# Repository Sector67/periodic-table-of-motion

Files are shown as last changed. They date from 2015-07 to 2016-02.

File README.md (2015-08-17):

# Periodic Table of Motion

## Overview

A science museum needs interactive exhibits, and this is an exhibit that can easily be extended, is easy to setup and install, is robust and safe and easy to maintain. Exhibits can easily cost tens of thousands of dollars, but this one can grow to any size budget but the top of the line is still under $4k. The idea is a periodic table of motion, where each cell, instead of an element, is a type of mechanical motion. Inside the cell is a description of the motion, a button to activate it, and an actual example of a working machine that uses the principle. Simple machines (lever, pulley, gear, etc.) are at the top of each column, and they increase in complexity. For an example of the variety of types of motions I want to capture and show off, see http://507movements.com. This project is very educational and interactive, and distills the basics of mechanics into individual and easy to understand concepts, building on them to show advanced motion and power transfer in a fun way.

## Structure

A cell is the basic independent unit. It has a title, description, machine class, and example use. It also has a physical manifestation which is described with 3D cad files and a bill of materials and build instructions. It also has code to control the display, written in Arduino for an ATTiny.

The repository has a section for cells, which are all based on the template cell. Each subfolder in the cells subfolder is used for a different cell. The template_cell can be copied and extended.

The underlying electronics and enclosure for a cell is defined in the cell subfolder. These instructions are used to build every cell. The cells folder is how to modify that cell to be unique.

The table is the large structure that contains the cells. This can be modified to suit the installation, but the repository contains a sample wall that is 5 cells tall, 12 wide, and contains all the parts necessary for the power supply as well.

The power supply is an ATX computer supply. Sufficiently large installations should use multiple supplies, possibly one for every 3-4 columns, as a typical behavior might be for kids to push all the buttons at once.

## Current Status

As of 2015/08/17, the template is complete. Electronics are done and verified, example sketches exist for each piece of hardware, the structure for the project is defined and template documents exist to enable individual cells to be created. A sample cell has been created to verify everything.

Still to do is designing each of the individual cells, building and assembling them, and raising the funds to produce more than a few cells. However, the template cell proves that it's all do-able. Designing the individual cells will take the longest; assembling won't be too bad.

## Cost

A rough estimate of the cost of this project is as follows:

Wall mount:
 * Power supplies 5 ATX: $100
 * Wood/Plastic $200
 * Cables $100

Cells x60:
 * Polycarb $5
 * Enclosure materials $10
 * Electronics $10
 * Motors/Servos $15
 * Plastic printed/machined parts $10
 * LED strip $5

So $4-500 for the main part and $55 per cell.

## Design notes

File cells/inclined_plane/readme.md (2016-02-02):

- Cell Title: Inclined Plane
- Description: One of the simple machines. Used to raise or lower a load. The ease of lifting or lowering an object is increased the longer the ramp is.
- Benefits: The same amount of work is done, but a lower force is applied over a greater distance.
- Used in: Highways, wheelchair access, slides. Two other simple machines can be derived from it; the wedge, and the screw.

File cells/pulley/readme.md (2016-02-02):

- Cell Title: Pulley
- Description: One of the simple machines. A free wheel translates force on a rope from one direction to another.
- Benefits: The pulley allows a force to be applied in a more convenient way, like lifting an object while staying stationary. When combined with a motor, the motor can spin a drum to collect the rope while it lifts or pulls the object.
- Used in: Elevators, cranes, and even window blinds benefit from pulleys.

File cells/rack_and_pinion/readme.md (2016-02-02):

- Cell Title: Rack and Pinion
- Description: A conversion from circular motion to linear motion. The spinning pinion pushes the linear gear, called a rack.
- Benefits: Very strong and accurate conversion. No slipping, but can be run backwards.
- Used in: Steering mechanisms, actuators.

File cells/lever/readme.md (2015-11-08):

- Cell Title: Lever - Class 1
- Description: One of the simple machines. Levers have three parts: fulcrum (pivot point), effort (where the force is applied), and resistance (where the weight is). The class 1 lever has the fulcrum in the middle, and by pushing down on one end the resistance is lifted.
- Benefits: The greater the ratio of the length, the more mechanical advantage. With a long effort arm, a huge weight can be lifted. This comes at a cost of distance. The effort arm must be pushed further to move the resistance just a little.
- Used in: Seesaw, crowbar, pliers

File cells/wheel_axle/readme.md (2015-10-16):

- Cell Title: Wheel and Axle
- Description: One of the simple machines. Transfers rotational motion between two different sized features to gain leverage or speed.
- Benefits: For every rotation, the wheel and axle spin the same number of degrees, but different distances. This difference is used to go fast, like on a car, or get leverage, like a door knob.
- Used in: Cars, bicycles, almost anything that spins.

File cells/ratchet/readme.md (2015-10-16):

- Cell Title: Ratchet
- Description: A spring-loaded prawl follows a spinning gear with special teeth so that it can only spin in one direction. When spun the opposite direction, the prawl presses agains the steep tooth and prevents the gear from spinning further.
- Benefits: Sometimes it is important to prevent something from going backwards, or to apply a force when spun direction but spin freely in the opposite direction (like a bike).
- Used in: Bicycles, roller coasters, zip ties, handcuffs

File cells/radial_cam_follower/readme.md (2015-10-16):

- Cell Title: Radial Cam Follower
- Description: A conversion from circular motion to linear motion along an axis perpendicular to the spinning. The piston is pressed against the cam by a spring or gravity, and as the cam rotates it pushes the follower up or down in a straight line.
- Benefits: Cams are used to do repetitive linear motion with a motor. The profile of the cam defines how fast (angle) or long (duration) or deep (lift) the linear motion is.
- Used in: Cars - the timing of valves opening and closing is done with the camshaft; a series of multiple radial cam followers.

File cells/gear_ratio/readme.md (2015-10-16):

- Cell Title: Gear Ratio - Big to Little
- Description: When gears are the same size, they turn at the same rate and transfer the same torque. When the driving gear is bigger, for every time it spins one revolution the small gear spins many times.
- Benefits: If very fast spinning is needed, a slower motor can use this gear configuration to get a fast output. This comes at a cost of torque.
- Used in: Bicycles - In higher gears you can go very fast, but it is difficult to go slow because you have no torque.

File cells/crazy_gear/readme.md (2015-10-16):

- Cell Title: Crazy Gear
- Description: Gears do not have to be perfectly symmectrical. Special gears can be made with very different teeth.
- Benefits: As long as the two gears mesh, they will work. The better they mesh, the smoother they will be. Certain kinds of teeth are better for more power transfer, others are good for speed or smoothness.
- Used in: There aren't many practical applications of this gear set, but gears of all types exist with varying designs suited to unique purposes.

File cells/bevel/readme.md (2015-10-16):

- Cell Title: Bevel Gear
- Description: A gear set that changes the axis of rotation. Usually 90 degree angles, but can be other angles. The spiral teeth allow for smoother engagement of each tooth.
- Benefits: Translates spinning motion. With different numbers of teeth, they can have mechanical advantage and drive with more or less torque and speed.
- Used in: Differential drives, like automobiles. The drive shaft connects to the back wheels of a rear wheel drive vehicle with bevel gears.

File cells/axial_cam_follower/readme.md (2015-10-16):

- Cell Title: Axial Cam Follower
- Description: A conversion from circular motion to linear motion. The spinning cam pushes the piston, which follows the profile of the surface.
- Benefits: Creates linear motion in the axis of revolution, making a long but narrow mechanism.
- Used in: Pumps. Pressure washers. The piston moves a fluid through a tube.

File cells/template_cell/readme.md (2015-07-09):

- Cell Title: {{name}}
- Machine Type: {{(one of) Lever, Wheel&Axle, Inclined Plane, Wedge, Screw, Pulley}}
- Description: {{short paragraph on what the machine does}}
- Used in: {{common uses}}

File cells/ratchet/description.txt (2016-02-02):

Cell Title: Template
Machine Type: (choose) Lever, Wheel&Axle, Inclined Plane, Wedge, Screw, Pulley
Description: (short paragraph on what the machine does)
Features: (short paragraph on how it is useful, advantages, disadvantages
Used in: (common uses)
Sponsored By: if sponsored, recognition

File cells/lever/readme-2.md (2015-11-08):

- Cell Title: Lever - Class 2
- Description: One of the simple machines. Levers have three parts: fulcrum (pivot point), effort (where the force is applied), and resistance (where the weight is). The class 2 lever has the resistance in the middle, the fulcrum at one end, and by lifting on the other end the resistance is lifted.
- Benefits: The greater the ratio of the length, the more mechanical advantage. With a long effort arm, a huge weight can be lifted. This comes at a cost of distance. The effort arm must be pushed further to move the resistance just a little.
- Used in: Wheelbarrow, nutcracker, bottle opener.

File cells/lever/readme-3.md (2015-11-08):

- Cell Title: Lever - Class 3
- Description: One of the simple machines. Levers have three parts: fulcrum (pivot point), effort (where the force is applied), and resistance (where the weight is). The class 3 lever has the resistance at one end, the fulcrum at the other end, and by pushing up in the middle, the resistance is lifted.
- Benefits: This is the opposite of the Class 2 lever because the mechanical advantage is always less than 1. This means a lot of effort is applied to raise the resistance, but the resistance moves up more distance. This is good when you need to translate power into speed.
- Used in: Tweezers, broom, hockey stick.

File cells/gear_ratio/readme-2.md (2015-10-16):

- Cell Title: Gear Ratio - Little to Big
- Description: When the driving gear is smaller, for every time it spins one revolution the large gear spins a fraction of a turn.
- Benefits: A fast but weak motor can drive very heavy loads with this type of gear because it trades speed for torque and very precise motion to a fraction of a degree. With the right ratios a motor spinning at a constant speed can spin one gear that does one revolution per minute, another that does one revolution per hour, and a third that does one revolution every 12 hours.
- Used in: Clocks, vehicles.

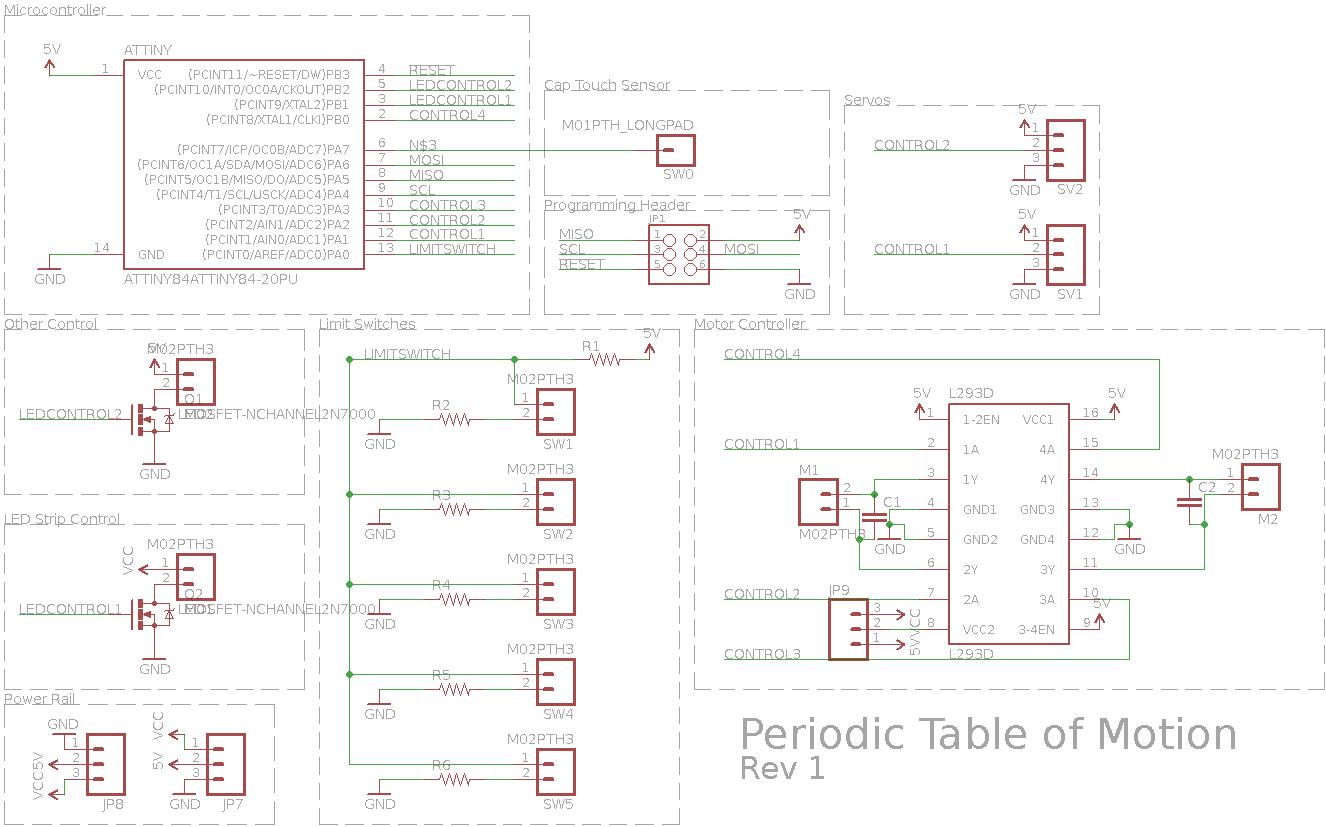
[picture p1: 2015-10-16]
cells/template_cell/electronics/schematic-rev1.png

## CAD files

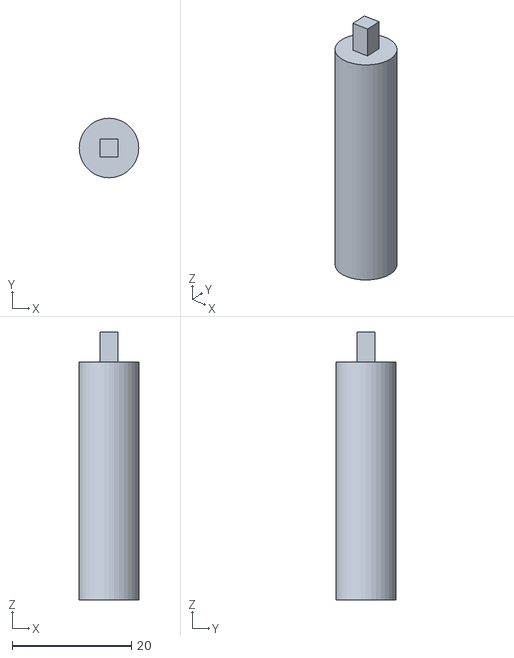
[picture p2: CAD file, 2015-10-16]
cells/wheel_axle/mechanical/Assembly - axle2-1.STL
10.00 x 10.0 x 45.0

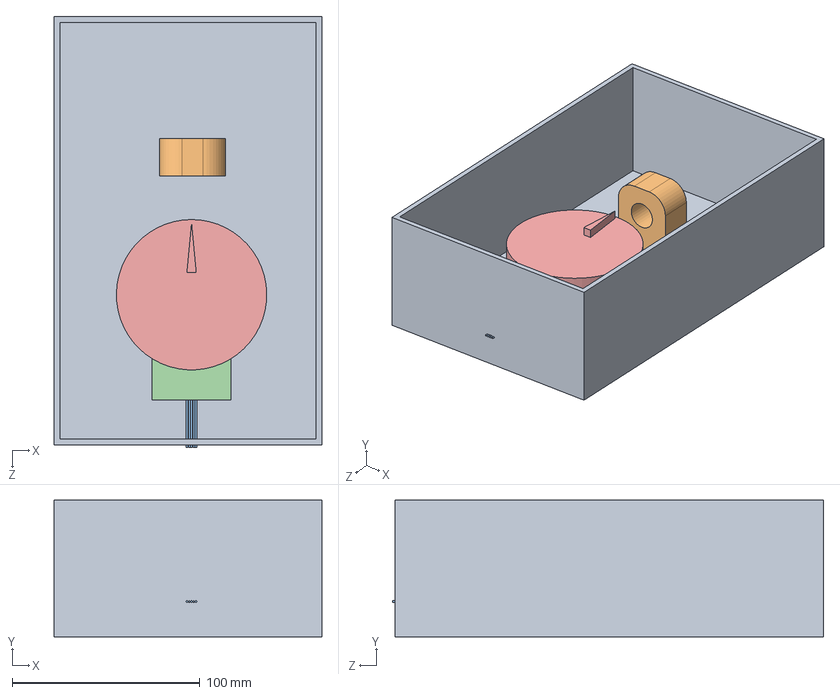
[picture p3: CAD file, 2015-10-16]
cells/radial_cam_follower/mechanical/Assembly.SLDASM
142.9 x 73.0 x 229.9 mm
Basic-ForSizing
piston_holder
Step Motor (28BYJ-48)
stepper_holder_28BYJ-48-flat
cam

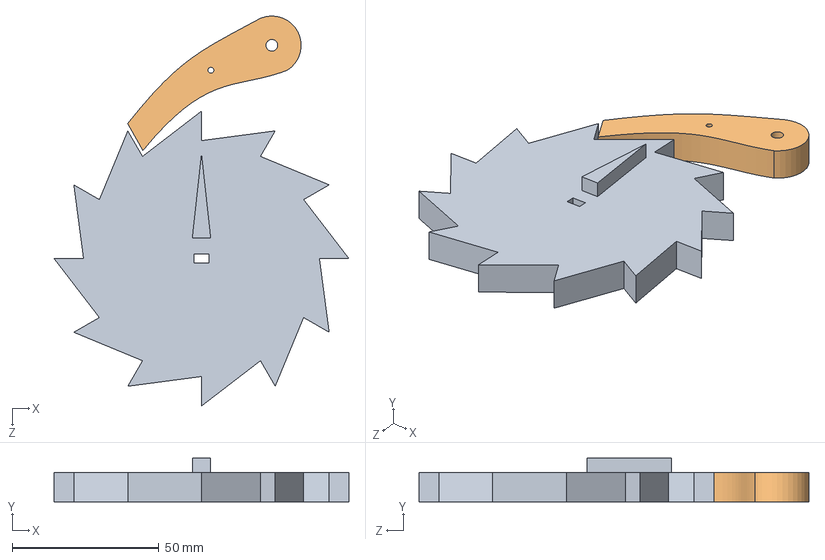
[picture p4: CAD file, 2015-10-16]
cells/ratchet/mechanical/Assembly.SLDASM
100.6 x 15.0 x 133.0 mm
Gear
Prawl

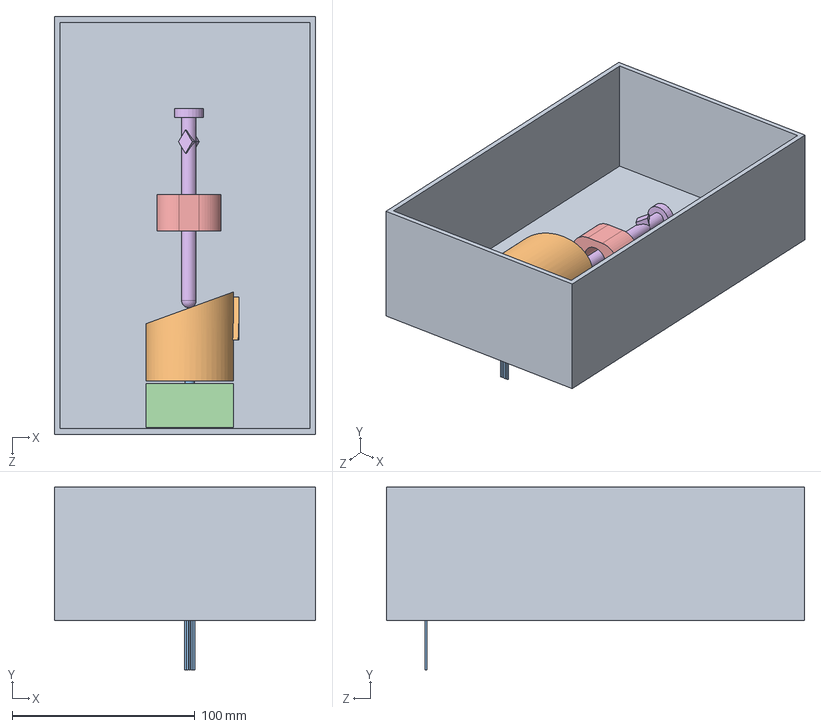
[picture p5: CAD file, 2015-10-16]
cells/axial_cam_follower/mechanical/Follower_Assembly.SLDASM
142.9 x 99.8 x 228.6 mm
Basic-ForSizing
cam
Step Motor (28BYJ-48)
stepper_holder_28BYJ-48
piston_holder
piston

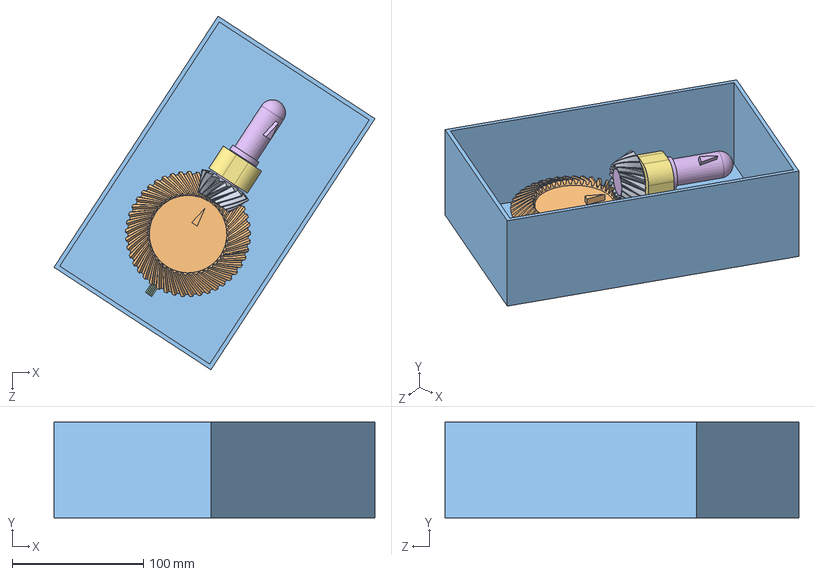
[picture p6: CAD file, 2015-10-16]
cells/bevel/mechanical/bevelgear_det_ass_mm_4LFQ4.sldasm
244.6 x 73.0 x 269.5 mm
bevelgear_det_pinion_mm_4LFQ4
bevelgear_det_wheel_mm_4LFQ4
Basic-ForSizing
Step Motor (28BYJ-48)
stepper_holder_28BYJ-48-flat
shaft
piston_holder

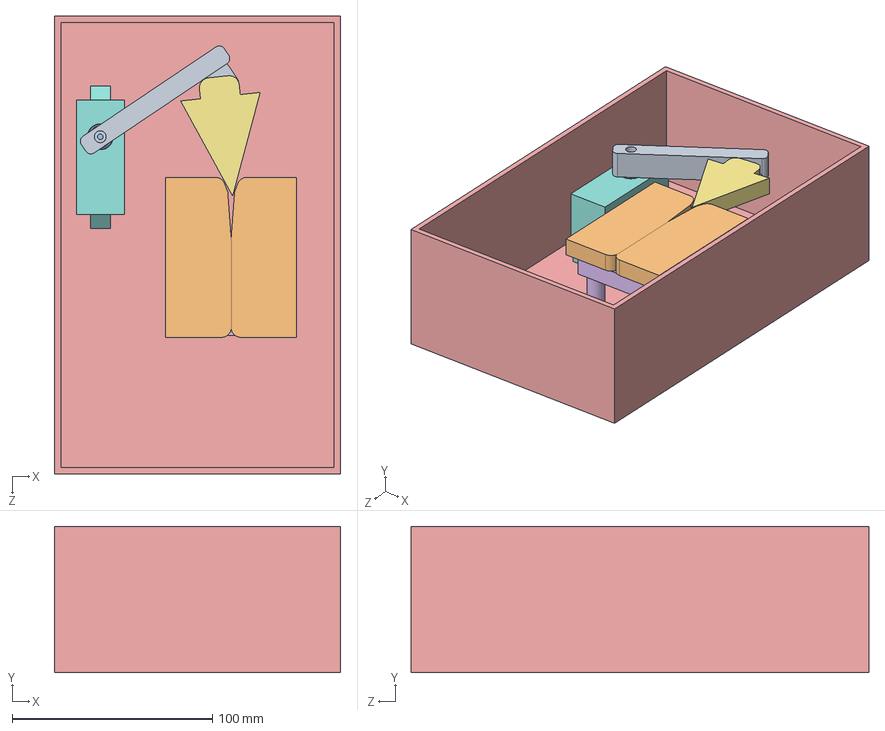
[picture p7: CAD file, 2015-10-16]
cells/wedge/mechanical/Assembly.SLDASM
142.9 x 73.0 x 228.6 mm
axe
block
servo body
servo output
Basic-ForSizing
block_holder
axe_head
servo_holder_hs422

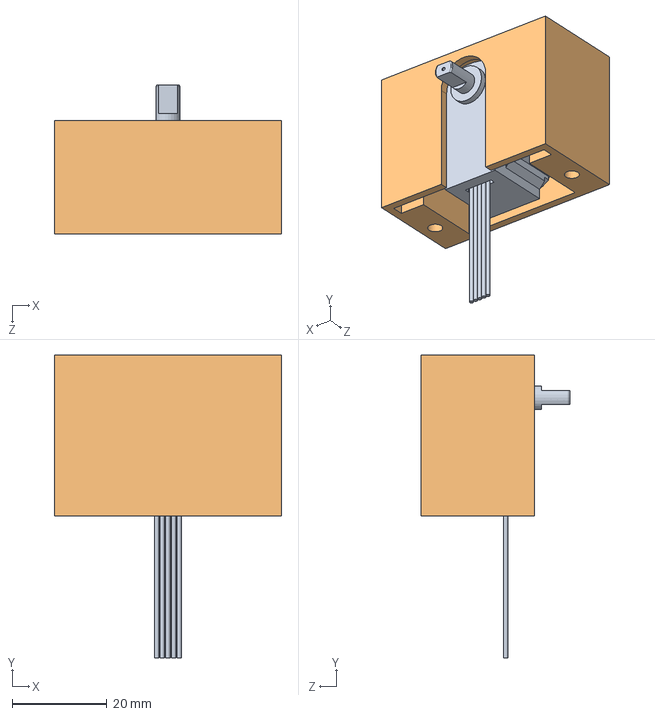
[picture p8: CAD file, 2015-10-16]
cells/template_cell/mechanical/stepper_holder.SLDASM
48.0 x 64.0 x 31.5 mm
Step Motor (28BYJ-48)
stepper_holder_28BYJ-48

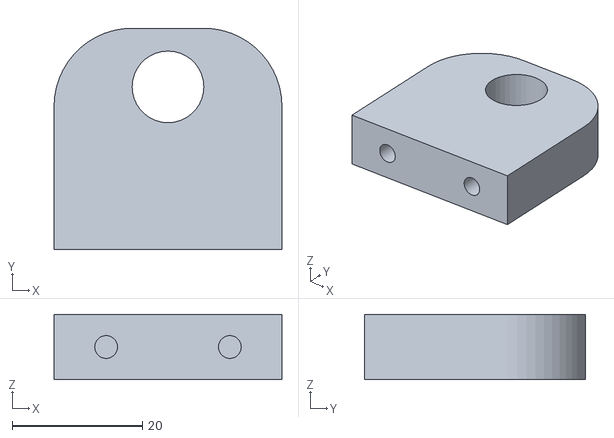
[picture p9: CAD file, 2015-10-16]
cells/wheel_axle/mechanical/Assembly - axle_holder-1.STL
35.0 x 34.0 x 10.00

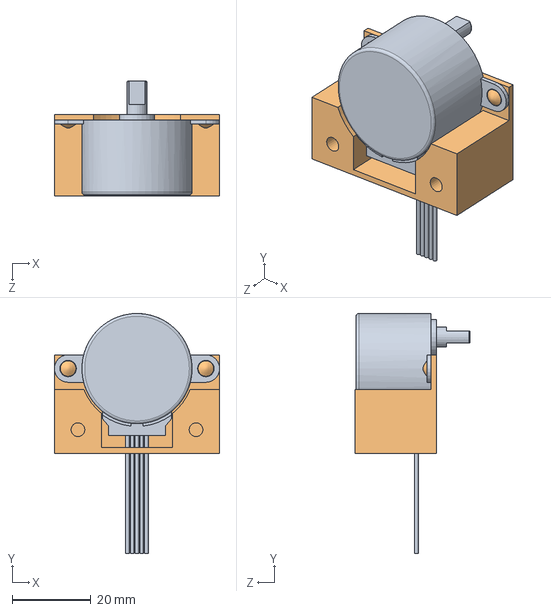
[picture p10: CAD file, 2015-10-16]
cells/template_cell/mechanical/stepper_holder_flat.SLDASM
42.0 x 61.0 x 29.3 mm
Step Motor (28BYJ-48)
stepper_holder_28BYJ-48-flat

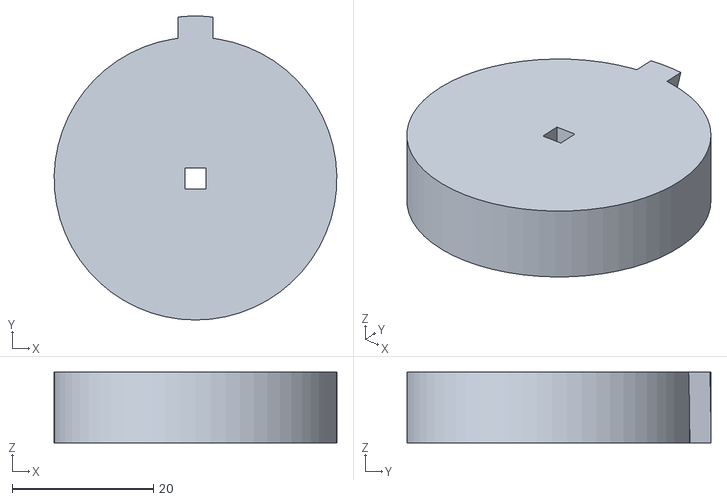
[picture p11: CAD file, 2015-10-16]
cells/wheel_axle/mechanical/Assembly - Wheel-1.STL
40.0 x 43.0 x 10.0

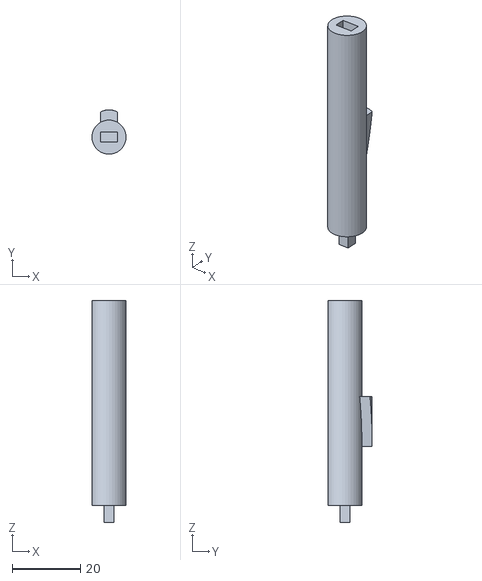
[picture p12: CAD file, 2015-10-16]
cells/wheel_axle/mechanical/Assembly - axle1-1.STL
10.00 x 13.0 x 65.0

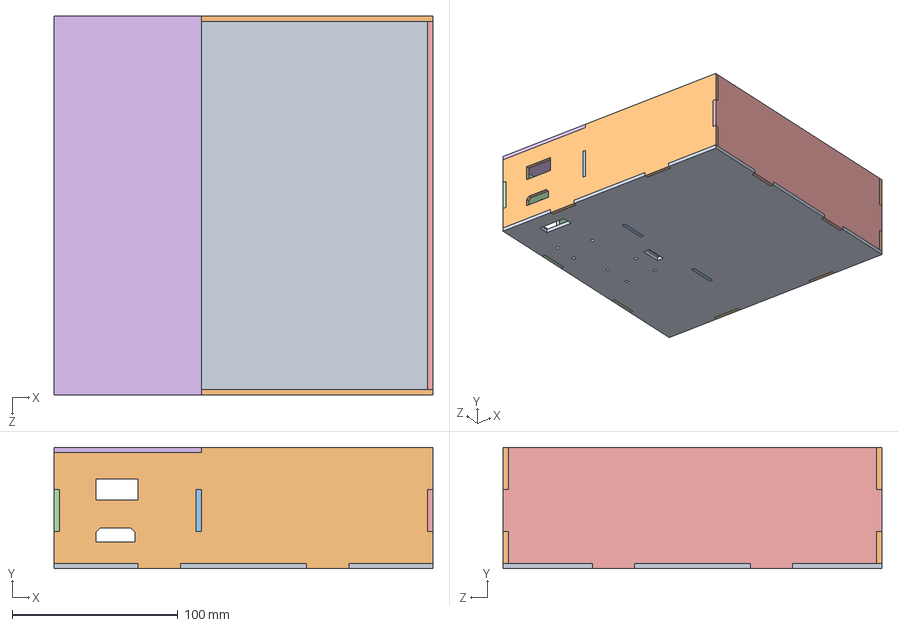
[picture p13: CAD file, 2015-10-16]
cells/template_cell/mechanical/Assembled.SLDASM
228.6 x 73.0 x 228.6 mm
CellBack
CellTopBottom x 2
CellCenter
CellLeft
CellRight

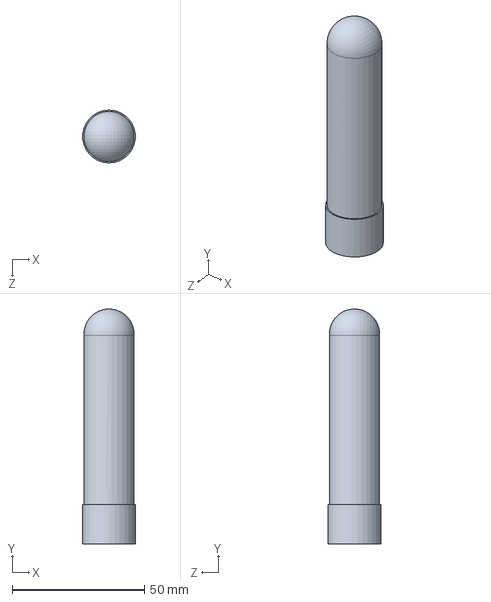
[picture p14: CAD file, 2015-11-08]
cells/bevel/mechanical/shaft.SLDPRT
19.9 x 89.0 x 20.0 mm

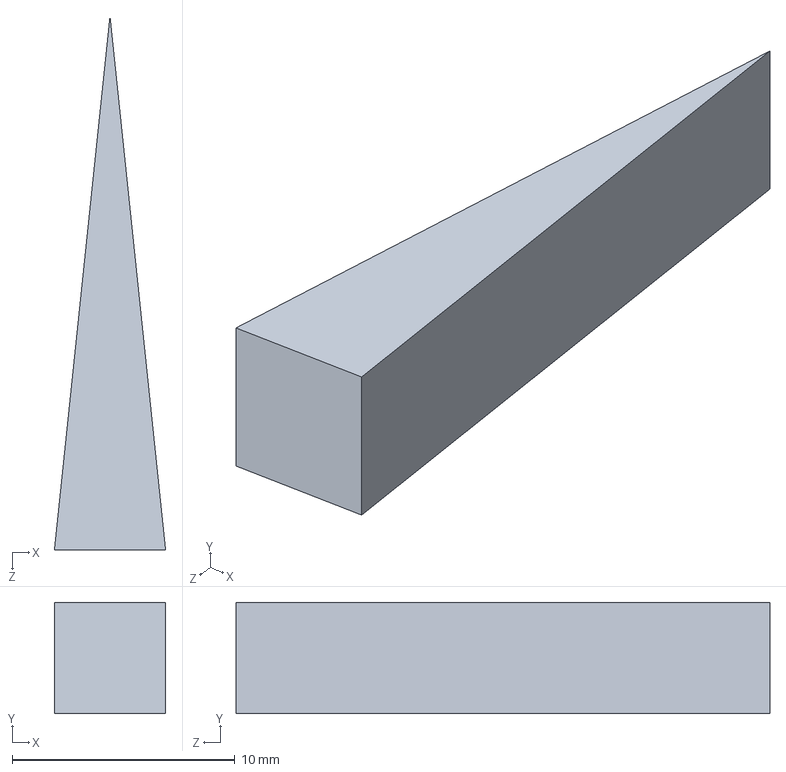
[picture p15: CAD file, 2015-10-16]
cells/crazy_gear/mechanical/indicator.SLDPRT
5.00 x 5.00 x 24.0 mm

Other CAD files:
cells/wheel_axle/mechanical/Assembly.SLDASM
cells/gear_ratio/mechanical/little_gear.SLDPRT
cells/radial_cam_follower/mechanical/cam.SLDPRT
cells/ratchet/mechanical/Gear.SLDPRT
cells/archimedes_screw/mechanical/Assembly.SLDASM
cells/archimedes_screw/mechanical/auger.SLDPRT
cells/archimedes_screw/mechanical/auger.STL
cells/archimedes_screw/mechanical/auger_bottom.STL
cells/archimedes_screw/mechanical/auger_holder.DXF
cells/archimedes_screw/mechanical/auger_holder.SLDPRT
cells/archimedes_screw/mechanical/auger_holder.STL
cells/archimedes_screw/mechanical/auger_top.STL
cells/archimedes_screw/mechanical/face.DXF
cells/archimedes_screw/mechanical/face.SLDPRT
cells/archimedes_screw/mechanical/slope.DXF
cells/archimedes_screw/mechanical/slope.SLDPRT
cells/archimedes_screw/mechanical/tube.SLDPRT
cells/axial_cam_follower/mechanical/cam.SLDPRT
cells/axial_cam_follower/mechanical/cam.STL
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

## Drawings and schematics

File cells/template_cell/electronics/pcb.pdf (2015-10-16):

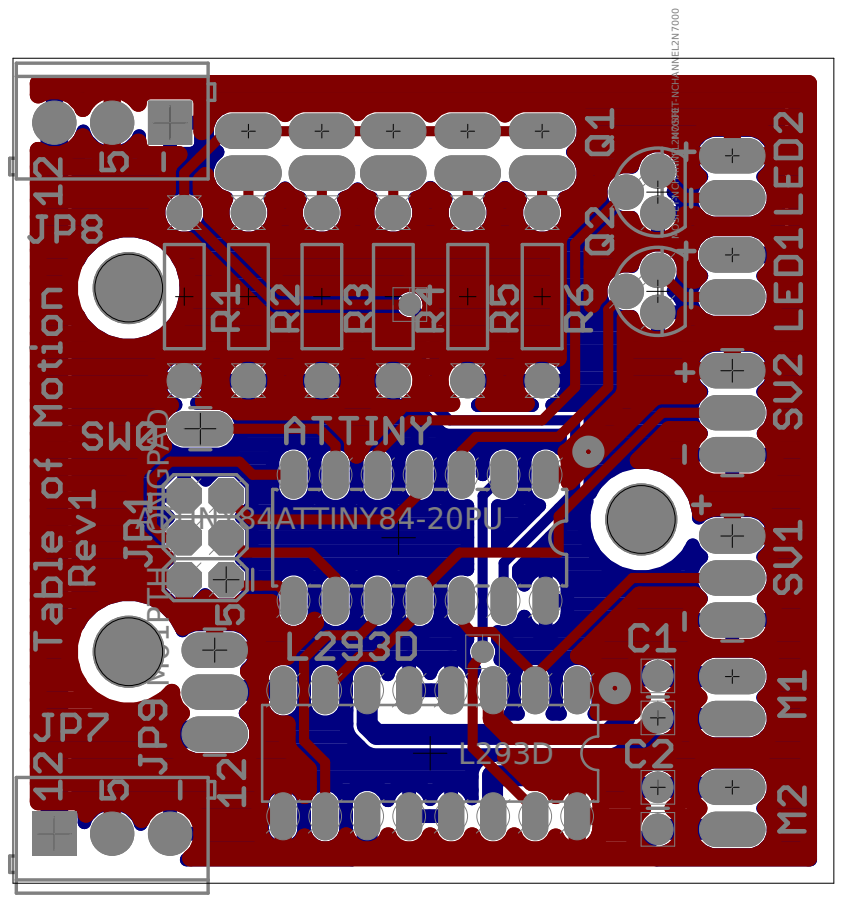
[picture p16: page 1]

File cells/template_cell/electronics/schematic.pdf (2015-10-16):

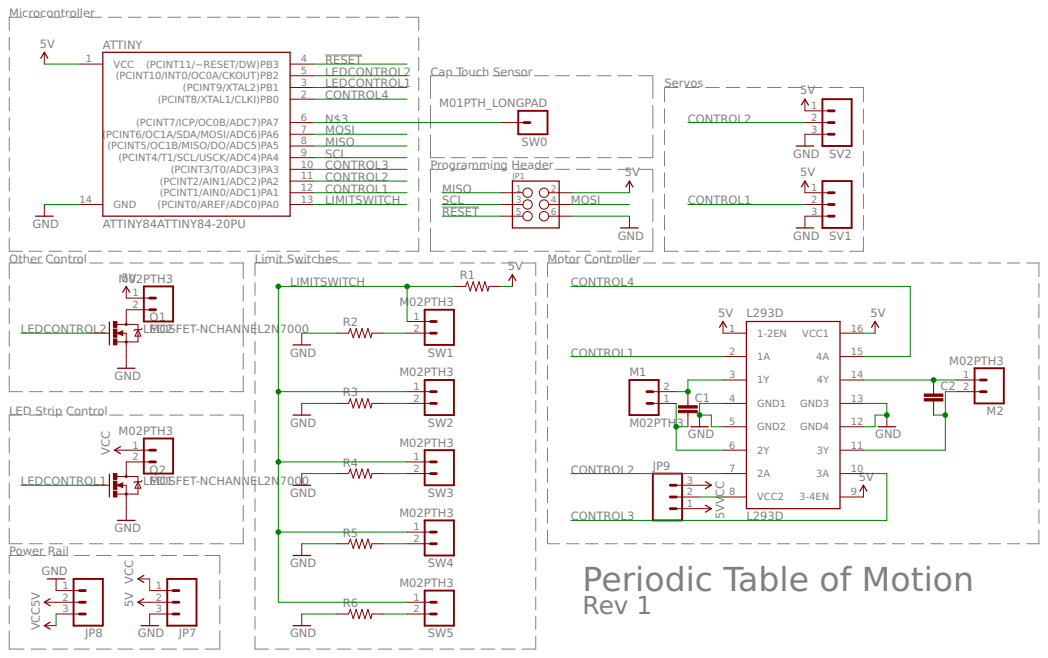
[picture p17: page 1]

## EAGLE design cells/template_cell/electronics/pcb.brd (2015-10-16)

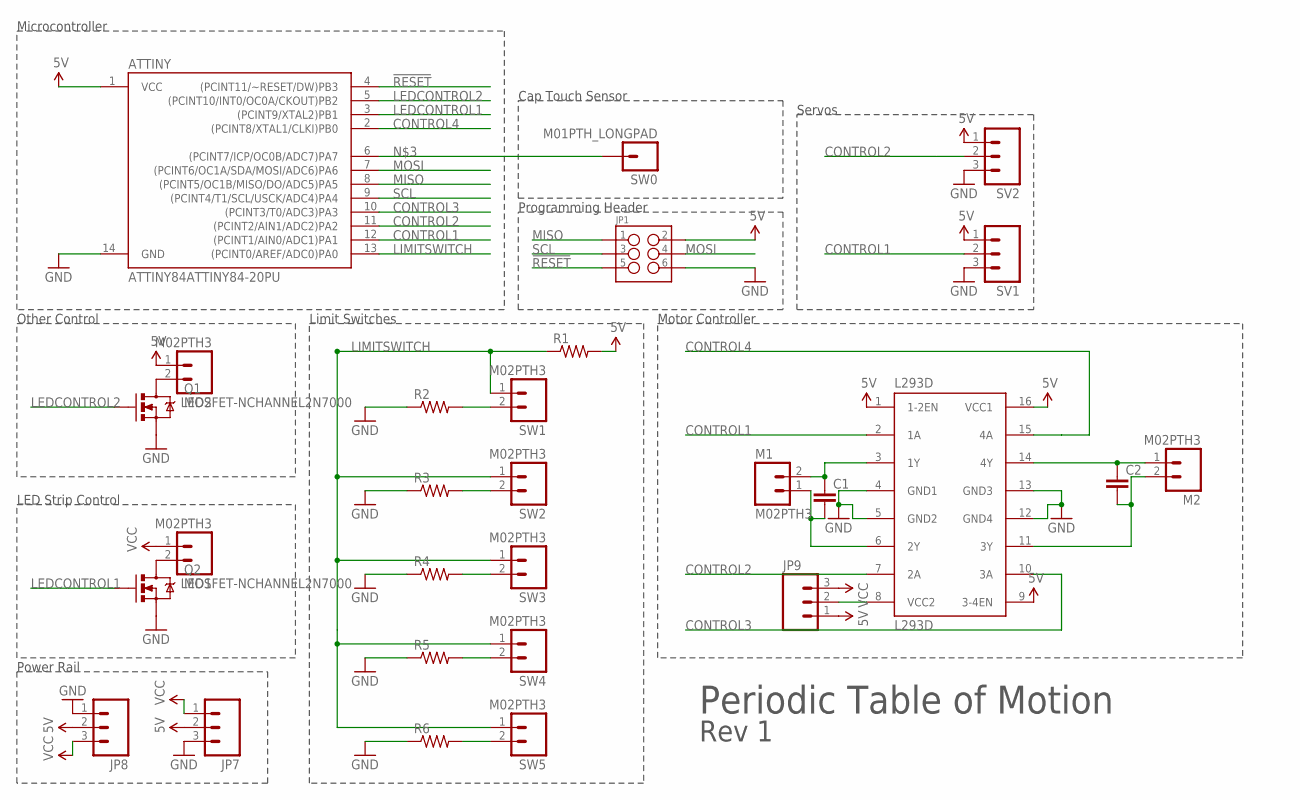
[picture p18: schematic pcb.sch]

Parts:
ATTINY: ATTINY84ATTINY84-20PU; DIL14
C1, C2: CAPPTH; CAP-PTH-SMALL
JP1: M03X22X3_SILK_MALE_PTH; 2X3
JP7, JP8: M03SCREW; SCREWTERMINAL-3.5MM-3
JP9: M03LONGPADS; 1X03_LONGPADS
L293D: L293D; DIL16
LED1, LED2: M02PTH3; 1X02_LONGPADS
M1, M2: M02PTH3; 1X02_LONGPADS
Q1, Q2: MOSFET-NCHANNEL2N7000; TO-92
R1, R2, R3, R4, R5, R6: RESISTORPTH-1/4W; AXIAL-0.4
SV1, SV2: M03LONGPADS; 1X03_LONGPADS
SW0: M01PTH_LONGPAD; 1X01_LONGPAD
SW1, SW2, SW3, SW4, SW5: M02PTH3; 1X02_LONGPADS

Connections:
5V: ATTINY.1 (VCC), JP1.2, JP7.2, JP8.2, JP9.1, L293D.1 (1-2EN), L293D.9 (3-4EN), L293D.16 (VCC1), LED2.1, R1.P$2 (2), SV1.1, SV2.1
!RESET: ATTINY.4 ((PCINT11/~RESET/DW)PB3), JP1.5
CONTROL1: ATTINY.12 ((PCINT1/AIN0/ADC1)PA1), L293D.2 (1A), SV1.2
CONTROL2: ATTINY.11 ((PCINT2/AIN1/ADC2)PA2), L293D.7 (2A), SV2.2
CONTROL3: ATTINY.10 ((PCINT3/T0/ADC3)PA3), L293D.10 (3A)
CONTROL4: ATTINY.2 ((PCINT8/XTAL1/CLKI)PB0), L293D.15 (4A)
GND: ATTINY.14 (GND), JP1.6, JP7.3, JP8.1, L293D.4 (GND1), L293D.5 (GND2), L293D.12 (GND4), L293D.13 (GND3), Q1.1 (S), Q2.1 (S), R2.P$1 (1), R3.P$1 (1), R4.P$1 (1), R5.P$1 (1), R6.P$1 (1), SV1.3, SV2.3
LEDCONTROL1: ATTINY.3 ((PCINT9/XTAL2)PB1), Q2.2 (G)
LEDCONTROL2: ATTINY.5 ((PCINT10/INT0/OC0A/CKOUT)PB2), Q1.2 (G)
LIMITSWITCH: ATTINY.13 ((PCINT0/AREF/ADC0)PA0), R1.P$1 (1), SW1.1, SW2.1, SW3.1, SW4.1, SW5.1
MISO: ATTINY.8 ((PCINT5/OC1B/MISO/DO/ADC5)PA5), JP1.1
MOSI: ATTINY.7 ((PCINT6/OC1A/SDA/MOSI/ADC6)PA6), JP1.4
unnamed: C2.1, L293D.14 (4Y), M2.1
unnamed: ATTINY.6 ((PCINT7/ICP/OC0B/ADC7)PA7), SW0.1
unnamed: C2.2, L293D.11 (3Y), M2.2
unnamed: C1.1, L293D.3 (1Y), M1.2
unnamed: C1.2, L293D.6 (2Y), M1.1
unnamed: R2.P$2 (2), SW1.2
unnamed: R3.P$2 (2), SW2.2
unnamed: JP9.2, L293D.8 (VCC2)
unnamed: LED1.2, Q2.3 (D)
unnamed: LED2.2, Q1.3 (D)
unnamed: R4.P$2 (2), SW3.2
unnamed: R5.P$2 (2), SW4.2
unnamed: R6.P$2 (2), SW5.2
SCL: ATTINY.9 ((PCINT4/T1/SCL/USCK/ADC4)PA4), JP1.3
VCC: JP7.1, JP8.3, JP9.3, LED1.1

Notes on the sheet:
Servos
Microcontroller
Power Rail
Motor Controller
Programming Header
LED Strip Control
Other Control
Limit Switches
Cap Touch Sensor
Periodic Table of Motion
Rev 1

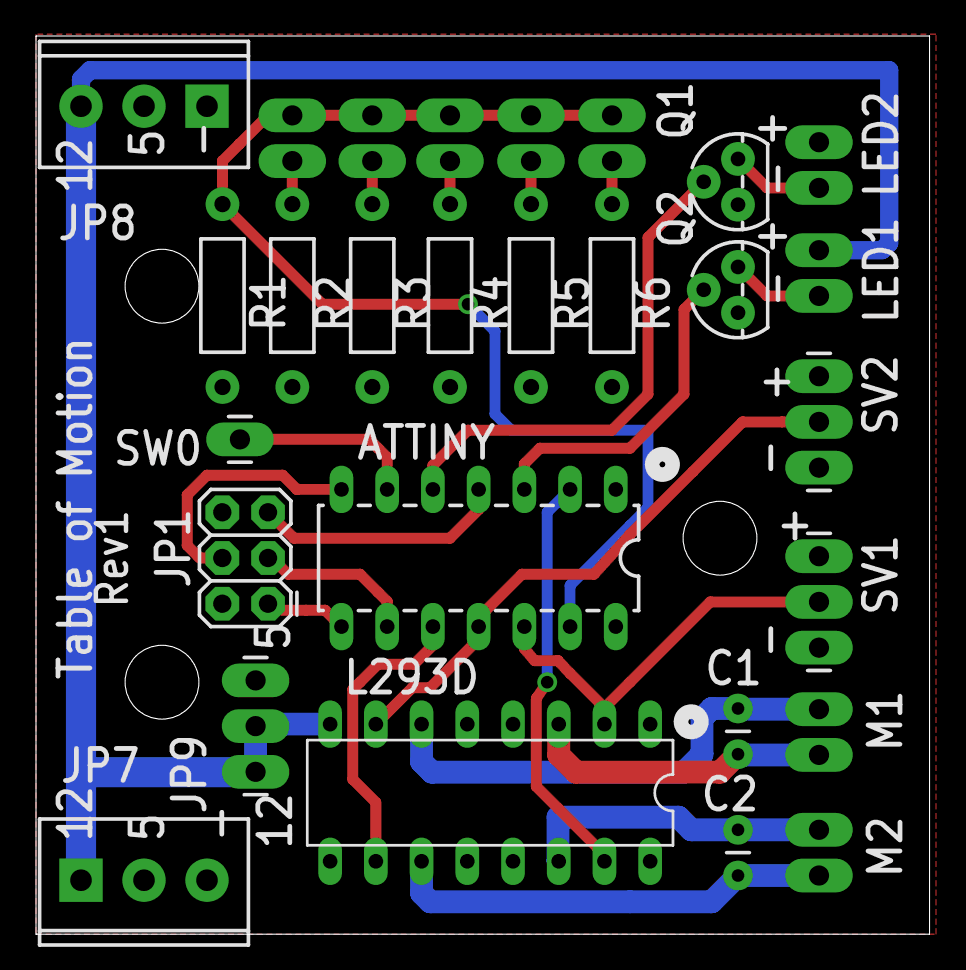
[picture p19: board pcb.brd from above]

Board: 2 copper layers, 49.6 x 49.9 mm, 28 parts (0 on the bottom side), 27 nets.

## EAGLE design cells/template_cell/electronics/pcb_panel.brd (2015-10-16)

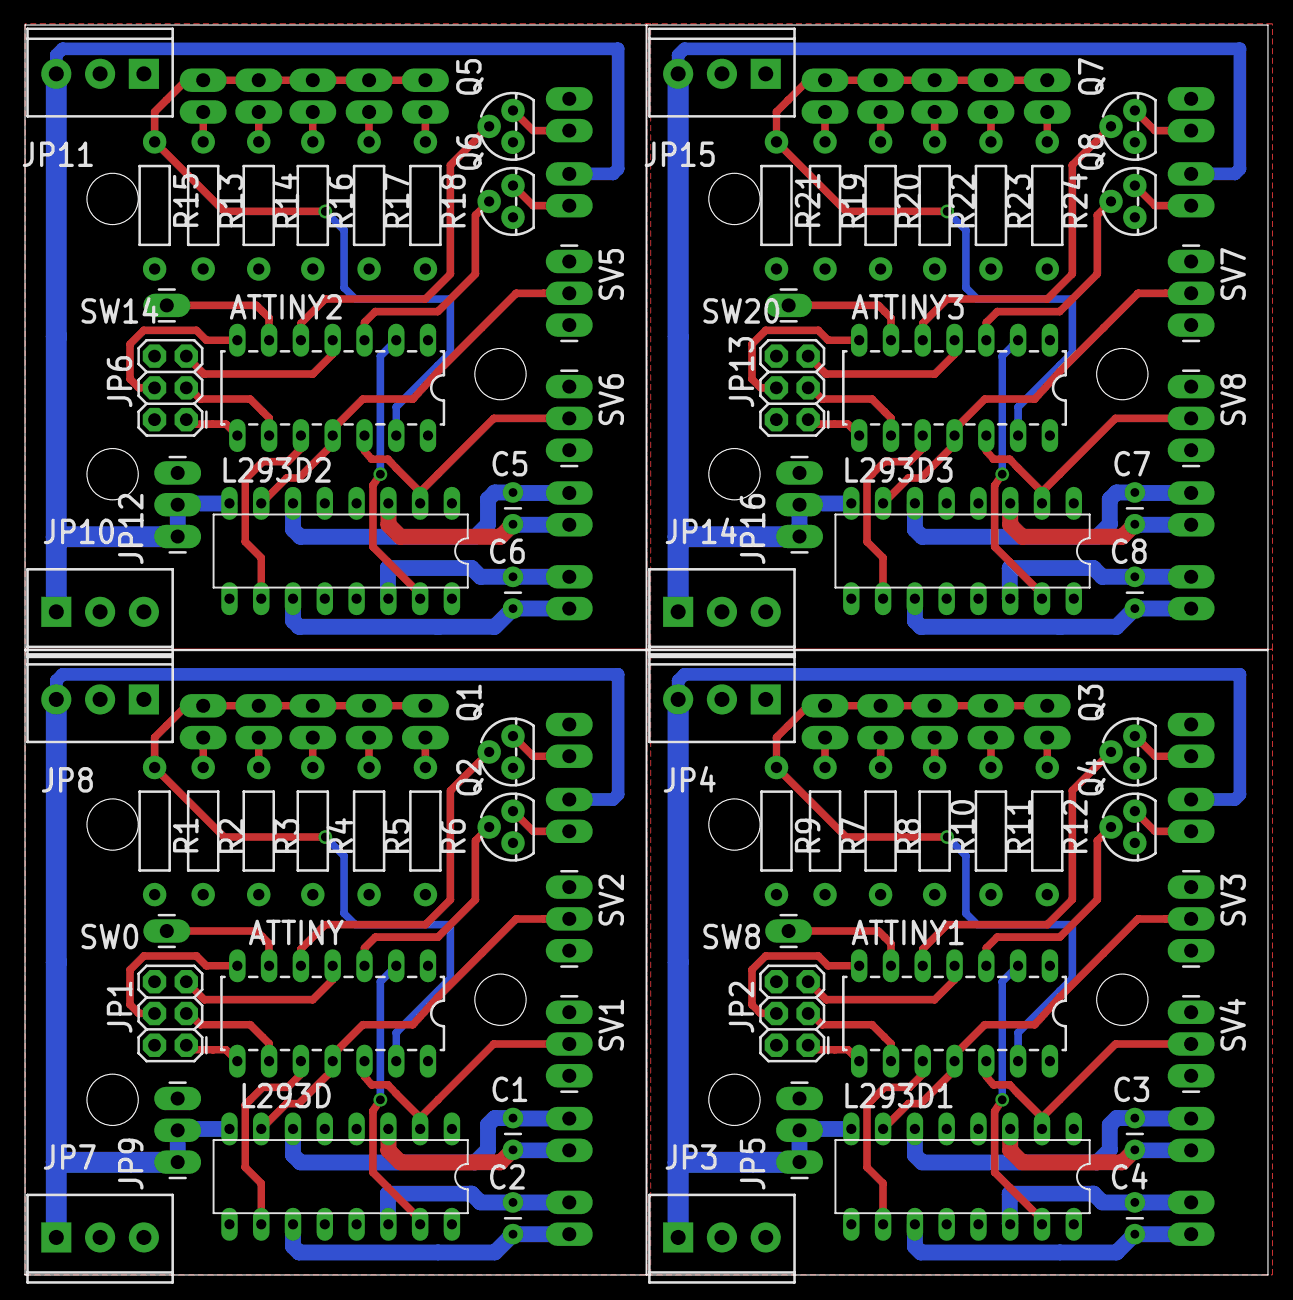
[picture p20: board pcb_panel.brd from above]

Board: 2 copper layers, 99.3 x 99.9 mm, 112 parts (0 on the bottom side), 108 nets.

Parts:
ATTINY, ATTINY1, ATTINY2, ATTINY3: ATTINY84ATTINY84-20PU; DIL14
C1, C2, C3, C4, C5, C6, C7, C8: CAP-PTH-SMALL
JP1, JP2, JP6, JP13: 2X3
JP3, JP4, JP7, JP8, JP10, JP11, JP14, JP15: SCREWTERMINAL-3.5MM-3
JP5, JP9, JP12, JP16: 1X03_LONGPADS
L293D, L293D1, L293D2, L293D3: L293D; DIL16
LED1, LED2, LED3, LED4, LED5, LED6, LED7, LED8: M02PTH3; 1X02_LONGPADS
M1, M2, M3, M4, M5, M6, M7, M8: M02PTH3; 1X02_LONGPADS
Q1, Q2, Q3, Q4, Q5, Q6, Q7, Q8: MOSFET-NCHANNEL2N7000; TO-92
R1, R2, R3, R4, R5, R6, R7, R8, R9, R10, R11, R12, R13, R14, R15, R16, R17, R18, R19, R20, R21, R22, R23, R24: AXIAL-0.4
SV1, SV2, SV3, SV4, SV5, SV6, SV7, SV8: 1X03_LONGPADS
SW0, SW8, SW14, SW20: M01PTH_LONGPAD; 1X01_LONGPAD
SW1, SW2, SW3, SW4, SW5, SW6, SW7, SW9, SW10, SW11, SW12, SW13, SW15, SW16, SW17, SW18, SW19, SW21, SW22, SW23: M02PTH3; 1X02_LONGPADS

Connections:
5V: ATTINY.1, JP1.2, JP7.2, JP8.2, JP9.1, L293D.1, L293D.9, L293D.16, LED2.1, R1.P$2, SV1.1, SV2.1
5V1: ATTINY1.1, JP2.2, JP3.2, JP4.2, JP5.1, L293D1.1, L293D1.9, L293D1.16, LED4.1, R9.P$2, SV3.1, SV4.1
5V2: ATTINY2.1, JP6.2, JP10.2, JP11.2, JP12.1, L293D2.1, L293D2.9, L293D2.16, LED6.1, R15.P$2, SV5.1, SV6.1
5V3: ATTINY3.1, JP13.2, JP14.2, JP15.2, JP16.1, L293D3.1, L293D3.9, L293D3.16, LED8.1, R21.P$2, SV7.1, SV8.1
!RESET: ATTINY.4, JP1.5
!RESET1: ATTINY1.4, JP2.5
!RESET2: ATTINY2.4, JP6.5
!RESET3: ATTINY3.4, JP13.5
CONTROL1: ATTINY.12, L293D.2, SV1.2
CONTROL2: ATTINY.11, L293D.7, SV2.2
CONTROL3: ATTINY.10, L293D.10
CONTROL4: ATTINY.2, L293D.15
CONTROL5: ATTINY1.12, L293D1.2, SV4.2
CONTROL6: ATTINY1.11, L293D1.7, SV3.2
CONTROL7: ATTINY1.2, L293D1.15
CONTROL8: ATTINY1.10, L293D1.10
CONTROL9: ATTINY2.12, L293D2.2, SV6.2
CONTROL10: ATTINY2.11, L293D2.7, SV5.2
CONTROL11: ATTINY2.2, L293D2.15
CONTROL12: ATTINY2.10, L293D2.10
CONTROL13: ATTINY3.12, L293D3.2, SV8.2
CONTROL14: ATTINY3.11, L293D3.7, SV7.2
CONTROL15: ATTINY3.2, L293D3.15
CONTROL16: ATTINY3.10, L293D3.10
GND: ATTINY.14, JP1.6, JP7.3, JP8.1, L293D.4, L293D.5, L293D.12, L293D.13, Q1.1, Q2.1, R2.P$1, R3.P$1, R4.P$1, R5.P$1, R6.P$1, SV1.3, SV2.3
GND1: ATTINY1.14, JP2.6, JP3.3, JP4.1, L293D1.4, L293D1.5, L293D1.12, L293D1.13, Q3.1, Q4.1, R7.P$1, R8.P$1, R10.P$1, R11.P$1, R12.P$1, SV3.3, SV4.3
GND2: ATTINY2.14, JP6.6, JP10.3, JP11.1, L293D2.4, L293D2.5, L293D2.12, L293D2.13, Q5.1, Q6.1, R13.P$1, R14.P$1, R16.P$1, R17.P$1, R18.P$1, SV5.3, SV6.3
GND3: ATTINY3.14, JP13.6, JP14.3, JP15.1, L293D3.4, L293D3.5, L293D3.12, L293D3.13, Q7.1, Q8.1, R19.P$1, R20.P$1, R22.P$1, R23.P$1, R24.P$1, SV7.3, SV8.3
LEDCONTROL1: ATTINY.3, Q2.2
LEDCONTROL2: ATTINY.5, Q1.2
LEDCONTROL3: ATTINY1.3, Q4.2
LEDCONTROL4: ATTINY1.5, Q3.2
LEDCONTROL5: ATTINY2.3, Q6.2
LEDCONTROL6: ATTINY2.5, Q5.2
LEDCONTROL7: ATTINY3.3, Q8.2
LEDCONTROL8: ATTINY3.5, Q7.2
LIMITSWITCH: ATTINY.13, R1.P$1, SW1.1, SW2.1, SW3.1, SW4.1, SW5.1
LIMITSWITCH1: ATTINY1.13, R9.P$1, SW6.1, SW7.1, SW9.1, SW10.1, SW11.1
LIMITSWITCH2: ATTINY2.13, R15.P$1, SW12.1, SW13.1, SW15.1, SW16.1, SW17.1
LIMITSWITCH3: ATTINY3.13, R21.P$1, SW18.1, SW19.1, SW21.1, SW22.1, SW23.1
MISO: ATTINY.8, JP1.1
MISO1: ATTINY1.8, JP2.1
MISO2: ATTINY2.8, JP6.1
MISO3: ATTINY3.8, JP13.1
MOSI: ATTINY.7, JP1.4
MOSI1: ATTINY1.7, JP2.4
MOSI2: ATTINY2.7, JP6.4
MOSI3: ATTINY3.7, JP13.4
unnamed: C2.1, L293D.14, M2.1
unnamed: ATTINY.6, SW0.1
unnamed: C4.1, L293D1.14, M3.1
unnamed: C2.2, L293D.11, M2.2
unnamed: C1.1, L293D.3, M1.2
unnamed: C1.2, L293D.6, M1.1
unnamed: C4.2, L293D1.11, M3.2
unnamed: C3.1, L293D1.3, M4.2
unnamed: C3.2, L293D1.6, M4.1
unnamed: R7.P$2, SW6.2
unnamed: R2.P$2, SW1.2
unnamed: R3.P$2, SW2.2
unnamed: R8.P$2, SW7.2
unnamed: ATTINY1.6, SW8.1
unnamed: LED3.2, Q4.3
unnamed: JP9.2, L293D.8
unnamed: LED1.2, Q2.3
unnamed: LED2.2, Q1.3
unnamed: LED4.2, Q3.3
unnamed: R10.P$2, SW9.2
unnamed: R4.P$2, SW3.2
unnamed: R11.P$2, SW10.2
unnamed: R5.P$2, SW4.2
unnamed: R12.P$2, SW11.2
unnamed: R6.P$2, SW5.2
unnamed: JP5.2, L293D1.8
unnamed: C6.1, L293D2.14, M5.1
unnamed: C6.2, L293D2.11, M5.2
unnamed: C5.1, L293D2.3, M6.2
unnamed: C5.2, L293D2.6, M6.1
unnamed: R13.P$2, SW12.2
unnamed: R14.P$2, SW13.2
unnamed: ATTINY2.6, SW14.1
unnamed: LED5.2, Q6.3
unnamed: LED6.2, Q5.3
unnamed: R16.P$2, SW15.2
unnamed: R17.P$2, SW16.2
unnamed: R18.P$2, SW17.2
unnamed: JP12.2, L293D2.8
unnamed: C8.1, L293D3.14, M7.1
unnamed: C8.2, L293D3.11, M7.2
unnamed: C7.1, L293D3.3, M8.2
unnamed: C7.2, L293D3.6, M8.1
unnamed: R19.P$2, SW18.2
unnamed: R20.P$2, SW19.2
unnamed: ATTINY3.6, SW20.1
unnamed: LED7.2, Q8.3
unnamed: LED8.2, Q7.3
unnamed: R22.P$2, SW21.2
unnamed: R23.P$2, SW22.2
unnamed: R24.P$2, SW23.2
unnamed: JP16.2, L293D3.8
SCL: ATTINY.9, JP1.3
SCL1: ATTINY1.9, JP2.3
SCL2: ATTINY2.9, JP6.3
SCL3: ATTINY3.9, JP13.3
VCC: JP7.1, JP8.3, JP9.3, LED1.1
VCC1: JP3.1, JP4.3, JP5.3, LED3.1
VCC2: JP10.1, JP11.3, JP12.3, LED5.1
VCC3: JP14.1, JP15.3, JP16.3, LED7.1

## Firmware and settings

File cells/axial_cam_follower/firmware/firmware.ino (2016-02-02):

#include <CapacitiveSensor.h>

CapacitiveSensor   cs_6_7 = CapacitiveSensor(6,7);        // 10M resistor between pins 6 & 7

int buttonReading;
int buttonState;             // the current reading from the input pin
int lastButtonState = LOW;   // the previous reading from the input pin

long lastDebounceTime = 0;  // the last time the output pin was toggled
long debounceDelay = 10;    // the debounce time; increase if the output flickers

//declare variables for the motor pins
int motorPin1 = 1;  // Blue   - 28BYJ48 pin 1
int motorPin2 = 2;  // Pink   - 28BYJ48 pin 2
int motorPin3 = 3;  // Yellow - 28BYJ48 pin 3
int motorPin4 = 10; // Orange - 28BYJ48 pin 4
                       // Red    - 28BYJ48 pin 5 (VCC)

int motorSpeed = 75;     //variable to set stepper speed

long runTime = 10000;  //how long the exhibit runs

//////////////////////////////////////////////////////////////////////////////
void setup() {
  cs_6_7.set_CS_AutocaL_Millis(0xFFFFFFFF);     // turn off autocalibrate
  pinMode(motorPin1, OUTPUT);
  pinMode(motorPin2, OUTPUT);
  pinMode(motorPin3, OUTPUT);
  pinMode(motorPin4, OUTPUT); 
}

//////////////////////////////////////////////////////////////////////////////
int i = 0;
int on = 0;
long total1;

void loop(){
    if (on == 1){
        clockwise();
        if ((millis() - lastDebounceTime) > debounceDelay+(runTime)) {
          on = 0;
          stop_motor();
        }
    }
    else if (on == 2){
        counterclockwise();
        if ((millis() - lastDebounceTime) > debounceDelay+runTime) {
          on = 0;
          stop_motor();
        }
    }
    else {    
      total1 =  cs_6_7.capacitiveSensor(120);
  
      if (total1>100){
        buttonReading = 1;
      }
      else {
        buttonReading = 0;
      }
      
    // If the switch changed, due to noise or pressing:
    if (buttonReading != lastButtonState) {
      // reset the debouncing timer
      lastDebounceTime = millis();
    } 
    
    if ((millis() - lastDebounceTime) > debounceDelay) {
      // whatever the reading is at, it's been there for longer
      // than the debounce delay, so take it as the actual current state:
  
      // if the button state has changed:
      if (buttonReading != buttonState) {
        buttonState = buttonReading;
  
        // only toggle the LED if the new button state is HIGH
        if (buttonState == HIGH) {
          on = 1;
        }
      }
    }
    lastButtonState = buttonReading;
  }
}

//////////////////////////////////////////////////////////////////////////////
//set pins to ULN2003 high in sequence from 1 to 4
//delay "motorSpeed" between each pin setting (to determine speed)
uint8_t bits1 = 0b11000001;
uint8_t bits2 = 0b01110000;
uint8_t bits3 = 0b00011100;
uint8_t bits4 = 0b00000111;


void counterclockwise (){
	uint8_t bits = 8;
	while (bits--){
		digitalWrite(motorPin1,bits1 & _BV(bits) ? HIGH : LOW);
		digitalWrite(motorPin2,bits2 & _BV(bits) ? HIGH : LOW);
		digitalWrite(motorPin3,bits3 & _BV(bits) ? HIGH : LOW);
		digitalWrite(motorPin4,bits4 & _BV(bits) ? HIGH : LOW);
		delayMicroseconds(motorSpeed);
	}
}

void clockwise (){
	uint8_t bits = 0;
	while (bits++<8){
		digitalWrite(motorPin1,bits1 & _BV(bits) ? HIGH : LOW);
		digitalWrite(motorPin2,bits2 & _BV(bits) ? HIGH : LOW);
		digitalWrite(motorPin3,bits3 & _BV(bits) ? HIGH : LOW);
		digitalWrite(motorPin4,bits4 & _BV(bits) ? HIGH : LOW);
		delayMicroseconds(motorSpeed);
	}
}

void stop_motor(){
 digitalWrite(motorPin4, LOW);
 digitalWrite(motorPin3, LOW);
 digitalWrite(motorPin2, LOW);
 digitalWrite(motorPin1, LOW);
 delayMicroseconds(motorSpeed);
}

/*
void counterclockwise (){
 // 1
 digitalWrite(motorPin1, HIGH);
 digitalWrite(motorPin2, LOW);
 digitalWrite(motorPin3, LOW);
 digitalWrite(motorPin4, LOW);
 delayMicroseconds(motorSpeed);
 // 2
 digitalWrite(motorPin1, HIGH);
 digitalWrite(motorPin2, HIGH);
 digitalWrite(motorPin3, LOW);
 digitalWrite(motorPin4, LOW);
 delayMicroseconds (motorSpeed);
 // 3
 digitalWrite(motorPin1, LOW);
 digitalWrite(motorPin2, HIGH);
 digitalWrite(motorPin3, LOW);
 digitalWrite(motorPin4, LOW);
 delayMicroseconds(motorSpeed);
 // 4
 digitalWrite(motorPin1, LOW);
 digitalWrite(motorPin2, HIGH);
 digitalWrite(motorPin3, HIGH);
 digitalWrite(motorPin4, LOW);
 delayMicroseconds(motorSpeed);
 // 5
 digitalWrite(motorPin1, LOW);
 digitalWrite(motorPin2, LOW);
 digitalWrite(motorPin3, HIGH);
 digitalWrite(motorPin4, LOW);
 delayMicroseconds(motorSpeed);
 // 6
 digitalWrite(motorPin1, LOW);
 digitalWrite(motorPin2, LOW);
 digitalWrite(motorPin3, HIGH);
 digitalWrite(motorPin4, HIGH);
 delayMicroseconds (motorSpeed);
 // 7
 digitalWrite(motorPin1, LOW);
 digitalWrite(motorPin2, LOW);
 digitalWrite(motorPin3, LOW);
 digitalWrite(motorPin4, HIGH);
 delayMicroseconds(motorSpeed);
 // 8
 digitalWrite(motorPin1, HIGH);
 digitalWrite(motorPin2, LOW);
 digitalWrite(motorPin3, LOW);
 digitalWrite(motorPin4, HIGH);
 delayMicroseconds(motorSpeed);
}

//////////////////////////////////////////////////////////////////////////////
//set pins to ULN2003 high in sequence from 4 to 1
//delay "motorSpeed" between each pin setting (to determine speed)

void clockwise(){
 // 1
 digitalWrite(motorPin4, HIGH);
 digitalWrite(motorPin3, LOW);
 digitalWrite(motorPin2, LOW);
 digitalWrite(motorPin1, LOW);
 delayMicroseconds(motorSpeed);
 // 2
 digitalWrite(motorPin4, HIGH);
 digitalWrite(motorPin3, HIGH);
 digitalWrite(motorPin2, LOW);
 digitalWrite(motorPin1, LOW);
 delayMicroseconds (motorSpeed);
 // 3
 digitalWrite(motorPin4, LOW);
 digitalWrite(motorPin3, HIGH);
 digitalWrite(motorPin2, LOW);
 digitalWrite(motorPin1, LOW);
 delayMicroseconds(motorSpeed);
 // 4
 digitalWrite(motorPin4, LOW);
 digitalWrite(motorPin3, HIGH);
 digitalWrite(motorPin2, HIGH);
 digitalWrite(motorPin1, LOW);
 delayMicroseconds(motorSpeed);
 // 5
 digitalWrite(motorPin4, LOW);
 digitalWrite(motorPin3, LOW);
 digitalWrite(motorPin2, HIGH);
 digitalWrite(motorPin1, LOW);
 delayMicroseconds(motorSpeed);
 // 6
 digitalWrite(motorPin4, LOW);
 digitalWrite(motorPin3, LOW);
 digitalWrite(motorPin2, HIGH);
 digitalWrite(motorPin1, HIGH);
 delayMicroseconds (motorSpeed);
 // 7
 digitalWrite(motorPin4, LOW);
 digitalWrite(motorPin3, LOW);
 digitalWrite(motorPin2, LOW);
 digitalWrite(motorPin1, HIGH);
 delayMicroseconds(motorSpeed);
 // 8
 digitalWrite(motorPin4, HIGH);
 digitalWrite(motorPin3, LOW);
 digitalWrite(motorPin2, LOW);
 digitalWrite(motorPin1, HIGH);
 delayMicroseconds(motorSpeed);
}*/

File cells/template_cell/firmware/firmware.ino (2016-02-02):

#include <CapacitiveSensor.h>

CapacitiveSensor   cs_6_7 = CapacitiveSensor(6,7);        // 10M resistor between pins 4 & 2, pin 2 is sensor pin, add a wire and or foil if desired

// Variables will change:
int buttonReading;
int buttonState;             // the current reading from the input pin
int lastButtonState = LOW;   // the previous reading from the input pin

// the following variables are long's because the time, measured in miliseconds,
// will quickly become a bigger number than can be stored in an int.
long lastDebounceTime = 0;  // the last time the output pin was toggled
long debounceDelay = 50;    // the debounce time; increase if the output flickers

int motor_left[] = {1, 2};
int motor_right[] = {3, 10};

int limit_switches = 1023;

long runTime = 4000;

void setup()                    
{
   cs_6_7.set_CS_AutocaL_Millis(0xFFFFFFFF);     // turn off autocalibrate on channel 1 - just as an example
   pinMode(8,OUTPUT); //MOSFET
   pinMode(9,OUTPUT); //MOSFET
   pinMode(1,OUTPUT); //MOTOR 1A
   pinMode(2,OUTPUT); //MOTOR 2A
   pinMode(3,OUTPUT); //MOTOR 3A
   pinMode(10,OUTPUT); //MOTOR 4A
}

void loop()                    
{
    delay(10);// arbitrary delay
    
    limit_switches = analogRead(0);
    
    if (limit_switches < 500){
      motor_stop(); 
    }
    else if (limit_switches < 800){
     drive_backward();
    }
    
    long total1 =  cs_6_7.capacitiveSensor(120);

    if (total1>100){
      buttonReading = 1;
    }
    else {
      buttonReading = 0;
    }
    
  // If the switch changed, due to noise or pressing:
  if (buttonReading != lastButtonState) {
    // reset the debouncing timer
    lastDebounceTime = millis();
  } 
  
  if ((millis() - lastDebounceTime) > debounceDelay) {
    // whatever the reading is at, it's been there for longer
    // than the debounce delay, so take it as the actual current state:

    // if the button state has changed:
    if (buttonReading != buttonState) {
      buttonState = buttonReading;

      // only toggle the LED if the new button state is HIGH
      if (buttonState == HIGH) {
        digitalWrite(8,HIGH);
        digitalWrite(9,LOW);
        drive_forward();
      }
    }
  }
  if ((millis() - lastDebounceTime) > debounceDelay+runTime) {
        digitalWrite(9,HIGH);
        digitalWrite(8,LOW);
        motor_stop();
  }
  lastButtonState = buttonReading;
}

void motor_stop(){
digitalWrite(motor_left[0], LOW); 
digitalWrite(motor_left[1], LOW); 

digitalWrite(motor_right[0], LOW); 
digitalWrite(motor_right[1], LOW);
delay(25);
}

void drive_forward(){
digitalWrite(motor_left[0], HIGH); 
digitalWrite(motor_left[1], LOW); 

digitalWrite(motor_right[0], HIGH); 
digitalWrite(motor_right[1], LOW); 
}

void drive_backward(){
digitalWrite(motor_left[0], LOW); 
digitalWrite(motor_left[1], HIGH); 

digitalWrite(motor_right[0], LOW); 
digitalWrite(motor_right[1], HIGH); 
}

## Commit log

2015-07-08 Initial commit
    Initial commit of cell, wall, and cell template.
    [pcb.brd, pcb.sch]
2015-07-09 Relaying out the board
    laying out the board again for production, easier to read, components
    aligned and placed better. ready for first rev production
    [pcb.brd, pcb.sch]
2015-10-16 Moving electronics folder to template_cell
    template_cell folder should contain all the things necessary to make a
    cell, including the generic things like the electronics and basic
    reusable parts.
    [pcb.brd, pcb.sch, pcb_panel.brd]
2015-10-16 Adding template cell enclosure and basic parts
    [Assembled.SLDASM, Basic-ForSizing.SLDPRT, Bottom.SLDPRT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]
2015-10-16 Adding Archimedes Screw cell
    [Assembly.SLDASM, auger.SLDPRT, auger.STL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]
2015-10-16 Adding Axial Cam Follower cell
    [Follower_Assembly.SLDASM, cam.SLDPRT, cam.STL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]
2015-10-16 Adding Bevel Gear cell
    [bevelgear_det_ass_mm_4LFQ4.sldasm, bevelgear_det_pinion_mm_4LFQ4.STL, bevelgear_det_pinion_mm_4LFQ4.sldprt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]
2015-10-16 Adding Crazy Gear cell
    Unfortunately, I don't have the design files for the original gears.
    These parts are just supplemental parts that allowed me to attach to the
    gear.
    [center_plug.SLDPRT, center_plug.STL, center_plug2.SLDPRT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]
2015-10-16 Adding Gear Ratio cell
    There are actually two cells here. One has a big to little ratio and the
    other is little to big.
    [big_gear.SLDPRT, big_gear.STL, little_gear.SLDPRT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]
2015-10-16 Adding Radial Cam Follower cell
    [Assembly.SLDASM, cam.SLDPRT, cam.STL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]
2015-10-16 Adding Ratchet Cell
    [Assembly.SLDASM, Gear.SLDPRT, Gear.STL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]
2015-10-16 Adding Wedge Cell
    [Assembly.SLDASM, axe.SLDPRT, axe.STL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]
2015-10-16 Adding Wheel and Axle cell
    [Assembly - Wheel-1.STL, Assembly - axle1-1.STL, Assembly - axle2-1.STL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]
2015-11-08 Redoing the bevel gear to have a bushing
    [piston_holder.SLDPRT, piston_holder.STL, shaft.SLDPRT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]

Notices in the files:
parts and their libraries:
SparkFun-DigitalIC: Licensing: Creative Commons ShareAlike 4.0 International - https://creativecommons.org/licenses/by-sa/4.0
